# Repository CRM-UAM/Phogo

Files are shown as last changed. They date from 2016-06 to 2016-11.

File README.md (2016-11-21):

# Phogo

Phogo is an educational project to learn how to program. It is based in the [Logo](https://en.wikipedia.org/wiki/Logo_(programming_language)) programming language (and its turtle), created in 1967 by Seymour Papert and other researchers.

_Phogo es un proyecto educativo para aprender a programar basado en el lenguaje de programación [Logo](https://en.wikipedia.org/wiki/Logo_(programming_language)) (y su tortuga) creado en 1967 por Seymour Papert y otros investigadores._

**You can find more information in the [project's wiki page](https://github.com/CRM-UAM/Phogo/wiki).**
Can't find what you are looking for? [Contact us](https://github.com/CRM-UAM/Phogo/issues/new).

***Toda la documentación está en la [wiki del proyecto](https://github.com/CRM-UAM/Phogo/wiki).***
_¿No encuentras algo? [Contacta con nosotros](https://github.com/CRM-UAM/Phogo/issues/new)._

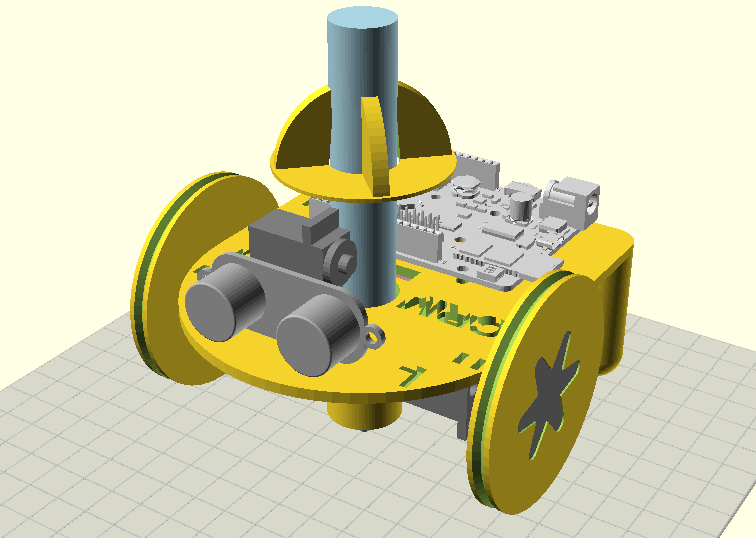
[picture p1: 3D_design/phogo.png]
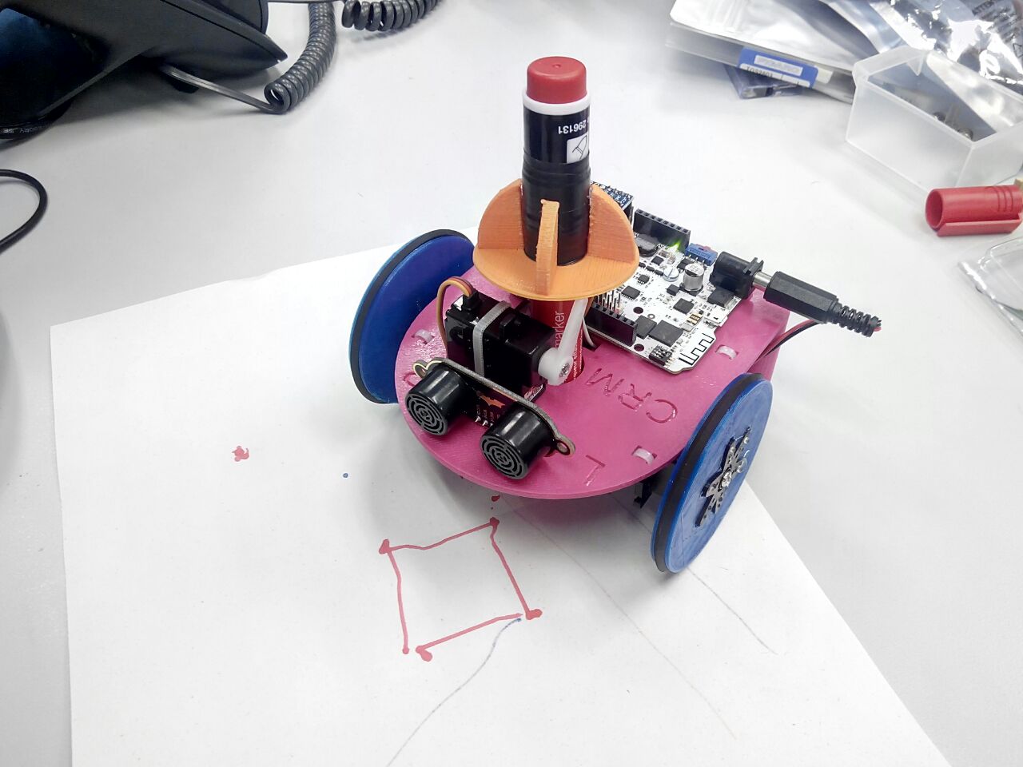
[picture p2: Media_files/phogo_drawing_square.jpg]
   
3D-printable CAD robot design. Find it in [3D_design](3D_design). _Diseño CAD imprimible en 3D. Puedes encontrarlo en [3D_design](3D_design)_

License
=

All of the Phogo source code is released under the [GNU General Public License Version 3](http://www.gnu.org/licenses/gpl-3.0.html).  
The rest of elements such as text, images or manuals are published under the [CC BY-SA 4.0 license terms](https://creativecommons.org/licenses/by-sa/4.0/).  

_Todo el código fuente de Phogo está publicado bajo una licencia [GNU General Public License Version 3](http://www.gnu.org/licenses/gpl-3.0.html)._  
_El resto de elementos como textos, imágenes o manuales bajo una licencia [CC BY-SA 4.0](https://creativecommons.org/licenses/by-sa/4.0/)._  

Authors
=

- Pablo Molins Ruano ([@molins](https://github.com/molins))
- Carlos González Sacristán ([@ChacheGS](https://github.com/ChacheGS))
- Carlos García Saura ([@CarlosGS](https://github.com/CarlosGS))

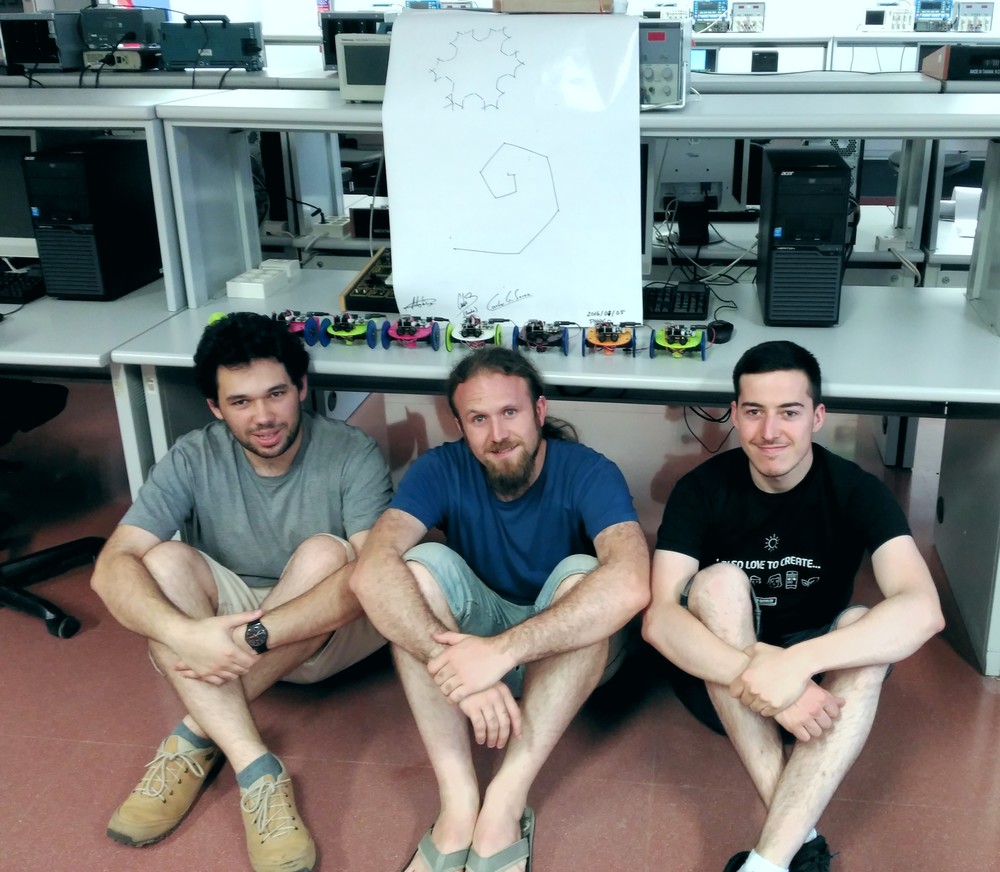
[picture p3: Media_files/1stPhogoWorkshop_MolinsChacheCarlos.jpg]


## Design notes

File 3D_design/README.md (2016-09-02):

Phogo 3D-printable design
=

Here you can find the [OpenScad](http://www.openscad.org/) source files for the Phogo mechanic parts.  
You may want to read the **[Bill of Materials & assembly guide](https://github.com/CRM-UAM/Phogo/wiki/Assembly-guide)** in the wiki.



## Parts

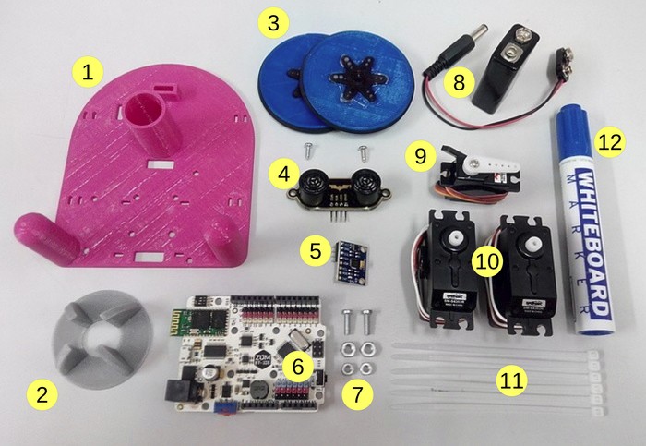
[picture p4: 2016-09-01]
Media_files/tutorial/assembly/1_all_parts_2.jpg

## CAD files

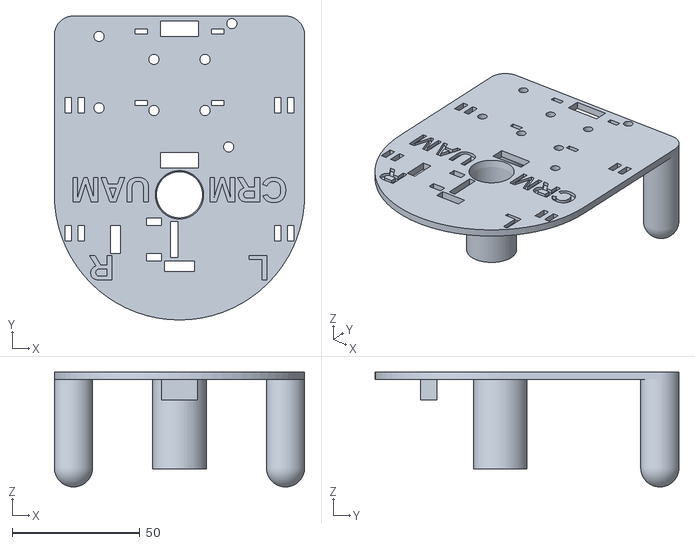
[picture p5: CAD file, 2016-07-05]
3D_design/phogo.stl
98.0 x 119.0 x 45.0

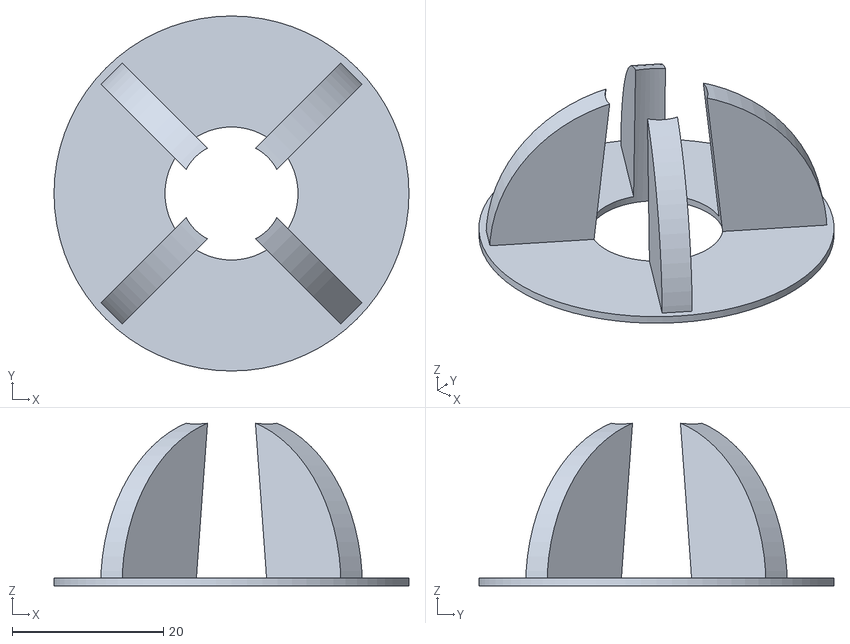
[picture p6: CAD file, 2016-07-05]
3D_design/pen_holder.stl
47.0 x 47.0 x 21.5

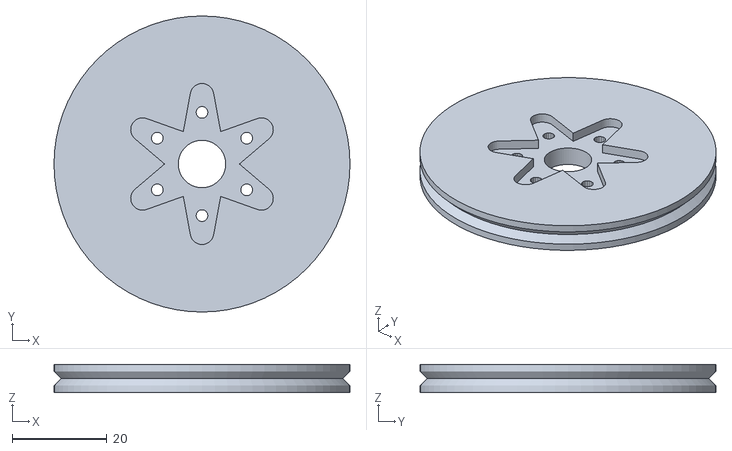
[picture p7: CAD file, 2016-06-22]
3D_design/wheel.stl
62.5 x 62.5 x 6.00

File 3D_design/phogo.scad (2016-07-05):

// This source file is part of the Phogo project
// https://github.com/CRM-UAM/Phogo
// Released under the GNU General Public License Version 3
// Club de Robotica-Mecatronica, Universidad Autonoma de Madrid, Spain



// Increase the resolution of default shapes
$fa = 5; // Minimum angle for fragments [degrees]
$fs = 0.5; // Minimum fragment size [mm]

use <libs/MCAD/servos.scad>
use <libs/Servo-wheel.scad>
use <libs/build_plate.scad>

wheel_diameter = 42;

floor_Z = -wheel_diameter;

pen_diameter = 17;
pen_len = 120;
pen_holder_tolerance = 0.5;
pen_holder_thickness = 2;
pen_holder_height = 35;
pen_tip_posZ = floor_Z;
pen_holder_Xoffset = 1;

servo_separation = 75+7;

chassis_thirdstand_diameter = 15;
chassis_thirdstand_height = -floor_Z-chassis_thirdstand_diameter/2;

chassis_thickness = 3;
chassis_width = servo_separation+2*8;
chassis_len = 70+chassis_width/2;
chassis_corner_radius = chassis_thirdstand_diameter/2;

screw_diam = 4; // diameter for tight fit

ultrasound_posY = -chassis_width/2+21;
ultrasound_support_len = 8;
ultrasound_support_X = 10;
ultrasound_support_Y = 2.5;
ultrasound_support_tolerance = 0.8;
ultrasound_support_thickness = 2;

module pen_support_vitamins() {
    color("lightblue") translate([0,0,pen_tip_posZ]) {
        translate([0,0,25]) cylinder(r=pen_diameter/2, h=pen_len-25);
        cylinder(r1=1.5,r2=pen_diameter/2+pen_holder_tolerance, h=25);
    }
    translate([-3+pen_holder_Xoffset,-8-pen_diameter/2,chassis_thickness])
        color("gray") alignds420([-18,0,17], [-90,0,-90]); // mini-servo para el rotulador
}

module pen_support(holes=false) {
    if(holes) {
        translate([0,0,pen_tip_posZ])
            cylinder(r=pen_diameter/2+pen_holder_tolerance, h=pen_len);
        cylinder(r1=pen_diameter/2+pen_holder_tolerance, r2=pen_diameter/2+2*pen_holder_tolerance, h=chassis_thickness+0.1);
        // Agujeros para sujetar el mini-servo
        translate([-3+pen_holder_Xoffset,-9-pen_diameter/2,0]) cube([3,14,chassis_thickness*3],center=true);
        translate([-11+pen_holder_Xoffset,-pen_diameter/2-2,0]) cube([6,3,chassis_thickness*3],center=true);
        translate([-11+pen_holder_Xoffset,-pen_diameter/2-16,0]) cube([6,3,chassis_thickness*3],center=true);
        // Agujero para el cable del mini-servo
        translate([-26+pen_holder_Xoffset,-9-pen_diameter/2,0]) cube([4,11,chassis_thickness*3],center=true);
        // Agujeros para los cables de la electronica
        translate([0,pen_diameter/2+pen_holder_thickness+6/2,0]) cube([15,6,chassis_thickness*3],center=true);
        translate([0,chassis_len-chassis_width/2-5,0]) cube([15,6,chassis_thickness*3],center=true);
    } else
        translate([0,0,-pen_holder_height])
            cylinder(r=pen_diameter/2+pen_holder_thickness, h=pen_holder_height+0.1);
}

module pen_holder() {
    translate([0,0,40])
        difference() {
            union() {
                cylinder(r=15+pen_diameter/2, h=1);
                difference() {
                    for(i=[-1,1]) rotate([90,0,45*i]) cylinder(r=14+pen_diameter/2, h=4, center=true);
                    rotate([180,0,0]) cylinder(r=15+pen_diameter/2, h=100);
                }
            }
            translate([0,0,-1]) cylinder(r1=pen_diameter/2+pen_holder_tolerance,r2=pen_diameter/2-4*pen_holder_tolerance, h=15+pen_diameter/2+2);
        }
    }

module continuous_rotation_servo(holes=false,wheel=false) {
    if(holes) {
        // Agujeros para las bridas
        translate([-2.5,-15,0]) cube([2.5,6,chassis_thickness*3],center=true);
        translate([2.5,-15,0]) cube([2.5,6,chassis_thickness*3],center=true);
        translate([-2.5,50-15,0]) cube([2.5,6,chassis_thickness*3],center=true);
        translate([2.5,50-15,0]) cube([2.5,6,chassis_thickness*3],center=true);
    } else {
        color("gray") futabas3003([-28,30,-20], [0,-90,180]);
        if(wheel) translate([12,0,-10]) rotate([0,90,0]) {
            Servo_wheel_6_arm_horn(); // Ruedas impresas
            color("gray") horn6(); // Soporte servo 6 brazos
        }
    }
}

module main_motors(holes=false,wheels=false) {
    translate([-servo_separation/2,0,0])
        mirror([1,0,0]) continuous_rotation_servo(holes,wheels);
    translate([servo_separation/2,0,0])
        continuous_rotation_servo(holes,wheels);
}

// From: https://github.com/Obijuan/printbot_part_library/tree/master/sensors/ultrasound
module ultrasound() {
    color("darkgray")
    translate([0,ultrasound_posY,0])
        translate([0,-4.5,14]) rotate([90,0,0]) import("libs/BAT-ultrasonic.stl");
}

module ultrasound_support(holes=false) {
    translate([0,ultrasound_posY,0])
        if(holes)
            cube([ultrasound_support_X+2*ultrasound_support_tolerance,ultrasound_support_Y+2*ultrasound_support_tolerance,ultrasound_support_len*3],center=true);
        else
            translate([0,0,-ultrasound_support_len/2+0.1]) cube([ultrasound_support_X+2*ultrasound_support_thickness,ultrasound_support_Y+2*ultrasound_support_thickness,ultrasound_support_len],center=true);
}

module battery(holes=false) {
    translate([0,50,0])
    if(holes) {
        translate([-15,14,0]) cube([5,2,chassis_thickness*3],center=true);
        translate([-15,-14,0]) cube([5,2,chassis_thickness*3],center=true);
        translate([15,14,0]) cube([5,2,chassis_thickness*3],center=true);
        translate([15,-14,0]) cube([5,2,chassis_thickness*3],center=true);
    } else {
        color("pink") translate([0,0,-15/2]) cube([52,25,15],center=true);
    }
}

// From: https://github.com/bq/zum/tree/master/zum-bt328/stl
module arduino(holes=false) {
    translate([0,43,2])
    if(holes) {
        translate([19.25,-24.25,0]) cylinder(r=screw_diam/2, h=chassis_thickness*5, center=true);
        translate([20.5,24,0]) cylinder(r=screw_diam/2, h=chassis_thickness*5, center=true);
        translate([-31.5,19,0]) cylinder(r=screw_diam/2, h=chassis_thickness*5, center=true);
        translate([-31.5,-9,0]) cylinder(r=screw_diam/2, h=chassis_thickness*5, center=true);
        for(i=[-1,1]) for(j=[-1,1]) translate([10*i,10*j,0]) cylinder(r=screw_diam/2, h=chassis_thickness*5, center=true);
    } else color("lightgray") translate([34.5,26.5,chassis_thickness+1.6]) rotate([0,0,180]) import("libs/zum_bt_328.stl");
}

module thirdstand() {
    for(i=[-1,1]) translate([i*(chassis_width/2-chassis_thirdstand_diameter/2),chassis_len-chassis_width/2-chassis_thirdstand_diameter/2,floor_Z+chassis_thirdstand_diameter/2]) union() {
            sphere(r=chassis_thirdstand_diameter/2);
            cylinder(r=chassis_thirdstand_diameter/2,h=chassis_thirdstand_height+0.1);
        }
}

module text_on_chassis() {
    translate([0,chassis_len-chassis_width/2-7,0])
    *rotate([0,0,180]) scale([1.5,1,1]) translate([0,0,chassis_thickness-1.5]) linear_extrude(height=10) {
        text("PHOGO",size=10,font="Liberation Sans",halign="center",valign="center",$fn=16);
    }
    translate([0,2,0])
    rotate([0,0,180]) translate([0,0,chassis_thickness-1.5]) linear_extrude(height=10) {
        text("CRM      UAM",size=10,font="Liberation Sans :style=Bold",halign="center",valign="center",$fn=16);
    }
    translate([0,-chassis_width/4-4,0])
    rotate([0,0,180]) translate([0,0,chassis_thickness-1.5]) linear_extrude(height=10) {
        text("L              R",size=10,font="Liberation Sans :style=Bold",halign="center",valign="center",$fn=16);
    }
}

module chassis() {
    difference() {
        union() {
            hull() {
                cylinder(r=chassis_width/2,h=chassis_thickness);
                translate([-chassis_width/2+chassis_corner_radius,chassis_len-chassis_width/2-chassis_corner_radius,0])
                    cylinder(r=chassis_corner_radius,h=chassis_thickness);
                translate([chassis_width/2-chassis_corner_radius,chassis_len-chassis_width/2-chassis_corner_radius,0])
                    cylinder(r=chassis_corner_radius,h=chassis_thickness);
            }
            pen_support();
            thirdstand();
            ultrasound_support();
        }
        pen_support(holes=true);
        main_motors(holes=true);
        ultrasound_support(holes=true);
        text_on_chassis();
        arduino(holes=true);
        battery(holes=true);
    }
}

module non_3D_printed() {
    main_motors(wheels=true);
    pen_support_vitamins();
    ultrasound();
    arduino();
    battery();
}

pen_holder();
chassis();
non_3D_printed();

//for display only, doesn't contribute to final object
translate([0,0,floor_Z]) build_plate(3,200,200);

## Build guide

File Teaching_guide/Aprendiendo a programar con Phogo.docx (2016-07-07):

# Aprendiendo a programar con Phogo

¿Alguna vez te has preguntado cómo es posible que Google sepa dónde encontrar cualquier cosa que busques en Internet? ¿Te has preguntado cómo funciona Minecraft? ¿Cómo sabe tu lavadora qué hacer para dejar tu ropa limpia? Son tres situaciones muy distintas pero las tres tienen en común la programación. Para que las tres funcionen, alguien ha programado un ordenador.

Programar es lo que hacemos los informáticos para dar instrucciones a un ordenador. Le decimos al ordenador qué tiene que hacer. Y el ordenador, si se lo hemos explicado bien, hace exactamente lo que le hemos dicho. Ahora vamos a aprender cómo hablarle al ordenador para que entienda.

Los ordenadores son como las personas en muchos aspectos. Por ejemplo, solo nos harán caso si hablamos un lenguaje que entiendan. Si a ti te hablan en chino, no harás caso, porque no entiendes chino. Si a un ordenador le hablas en español, no te entiende. Por eso nos toca aprender un nuevo lenguaje para hablar con el ordenador.

El lenguaje que vamos a aprender se llama Python. Se parece un poquito al inglés, pero solo un poco. Para que sea más divertido, al ordenador le hemos dado una tortuga. La tortuga es tan obediente como el ordenador. ¡Si sabemos cómo darle órdenes!

Aquí van dos foto de la tortuga. La tuya puede que tenga un color distinto, pero es igual en todo lo demás:

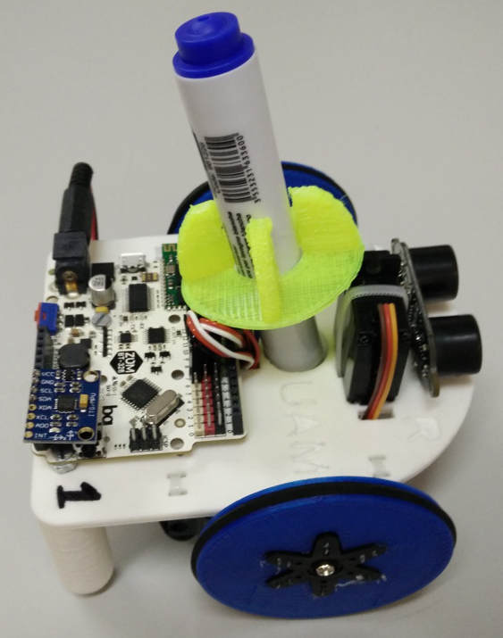
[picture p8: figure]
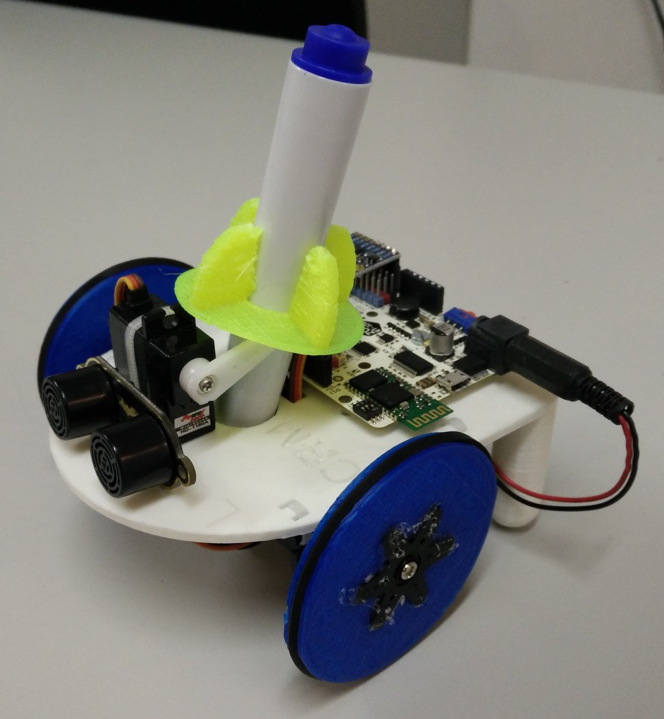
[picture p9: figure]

# Cómo hablar con el ordenador

Para hablar con el ordenador vamos a usar un programa que se llama Idle. Ya deberías tenerlo abierto en tu ordenador. Si no está abierto, o se cerrara en algún momento, pide ayuda a un monitor para volver a abrirlo.

El programa tiene dos ventanas:

1. A la derecha, la ventana de instrucciones, donde tú escribirás lo que quieras decirle al ordenador.
2. A la izquierda, la ventana de resultados, donde el ordenador te dirá qué va haciendo.

¿Has visto que en la ventana de instrucciones, arriba del todo, aparece from crmphogo import *? A esa frase la llamamos el saludo. Es importante que aparezca en todos los programas que escribas que quieran hablar con la tortuga, porque es la manera que tenemos de decirle al ordenador que queremos hablar con la tortuga. Si no lo ponemos y le damos órdenes para la tortuga, el ordenador no nos entenderá y nos dirá que no nos entiende la ventana de resultados.

Recuerda que el ordenador habla un idioma raro. Si aparece algo en la ventana de resultados que no entiendes y la tortuga no hace lo que quieres, pregunta a un monitor, que sabe cómo entender al ordenador.

Hemos aprendido ya muchas cosas:

- Que en el programa hay dos ventas:
  1. A la derecha, la venta de instrucciones, donde le contamos al ordenador qué tiene que hacer.
  2. A la izquierda, la venta de resultados, donde el ordenador nos cuenta qué tal le va cumpliendo nuestras órdenes.
- La tortuga necesita un saludo cada vez: from crmphogo import *
- Si tenemos algún problema, podemos pedir ayuda a los monitores, en cualquier momento

# Aprendiendo a moverse

Vamos a empezar con algo fácil. Vamos a hacer que la tortuga se mueva. Prueba a escribir forward() en la ventana de instrucciones, debajo del saludo. forward() en inglés significa “hacia delante” (así que la tortuga debería moverse hacia delante). Cuando lo hayas escrito, deberías tener algo así en tu ventana de instrucciones:

from crmphogo import *

forward()

Una vez hemos terminado de escribir tenemos que decirle al ordenador que ya hemos terminado y queremos que empiece a hacer lo que hemos puesto. Para eso, pulsa F5 (una tecla que está arriba en tu teclado). Deberías ver en la ventana de resultados una tortuga dibujada y al ordenador diciéndole a la tortuga que tiene que ir hacia delante (FD en el lenguaje de la tortuga). Cuando la tortuga termine de andar, le dirá que todo ha ido bien. Le dirá OK al ordenador.

¿Se ha movido la tortuga? Si no lo ha hecho, pide ayuda a alguno de los monitores. Si lo ha hecho… ¡has escrito tu primer programa!

La tortuga, como toda tortuga que se precie, no sólo puede moverse hacia delante. Borra forward() y prueba a escribir back(). Deberías tener algo así en tu ventana de instrucciones:

from crmphogo import *

back()

Fíjate que seguimos poniendo el saludo. Es importante que lo pongamos cada vez. ¿Qué ha hecho la tortuga? ¿Y qué pasa cuando borras back() y escribes right() o left()? ¡Pruébalo! Y recuerda pulsar F5 cada vez que quieras que el ordenador haga lo que hayas escrito en la ventana de instrucciones.

Si la tortuga solo pudiera girar 90º grados sería una tortuga mala. Como la nuestra no es una tortuga mala, puede girar tantos grados como quieras. ¿Cómo? Prueba a escribir en tu ventana de instrucciones lo siguientes:

from crmphogo import *

right(45)

left(180)

right(270)

Y fíjate en lo que pasa…

forward() y back() también pueden escribirse con un número dentro. Prueba a que tu ventana de instrucciones tenga el siguiente código:

from crmphogo import *

forward(5)

back(20)

forward(15)

Y observa qué ocurre…

Si has llegado hasta aquí, ahora sabrás cómo mover a la tortuga:

- Si escribes forward() avanzará.
- Si escribes back(), retrocederá.
- Si escribes right() girará a la derecha
- Con left() girará a la izquierda.

También sabrás que puedes escribir las ordenes con más información:

- Si escribes right(grados) la tortuga girará hacia la derecha tantos grados como hayas dicho.
- Si no pones nada, girará 90º.
- Lo mismo con left() (pero girando a la izquierda).
- foward(número) avanzan tantos centímetros como le hayas dicho.
- Si no escribes un número avanzará 10 cm.
- Igual para back() (solo que yendo hacia atrás).

# Aprendiendo a dibujar

Que la tortuga se mueva es divertido, pero más divertido es que pinte. Si te fijas en tu tortuga, tiene un rotulador. Podemos pedirle a la tortuga que utilice el rotulador para ir pintando allí por donde vaya. Vamos a probarlo.

Asegúrate de que tu tortuga está encima de un papel. Escribe, justo después del saludo, pen_down() y luego algo que haga que la tortuga se mueva. pen_down() significa “rotulador abajo” y es la manera de decirle a la tortuga que vaya pintando.

Con esto, ¿sabrías cómo dibujar un cuadrado? ¡Inténtalo!

Puede que en algunos dibujos, quieras que la tortuga se mueva por algún sitio sin dejar rastro. Que deje de pintar. Para eso escribe pen_up() que significa “rotulador arriba”. Al subirlo deja de apoyarse en el papel, y ya no se ve.

¿Podrías dibujar un cuadrado, pero ahora con líneas discontinuas? Algo así:

Con esto puedes dibujar muchas cosas distintas. ¡A ver qué se te ocurre! Dibuja todas ellas. Mira que ha hecho el resto, y si hay algo te gusta, ¡intenta dibujarlo tú!

La tortuga ya no solo se mueve, ¡ahora también dibuja!

- Si escribes pen_down() empezará a dibujar.
- Si escribes pen_up() dejará de hacerlo.

Acuérdate de poner la tortuga sobre papel, si va a pintar.

# Aprendiendo a repetir

Nota: Esta parte puede ser un poco complicada. Léela solo si quieres. Pregunta si tienes dudas.

¿Te acuerdas del cuadrado que has hecho al principio? Debes haber escrito en la ventana de instrucciones algo parecido a esto:

from crmphogo import *

forward()

right()

forward()

right()

forward()

right()

forward()

right()

Te has fijado en que las líneas se repiten, ¿verdad? Hay una manera de escribir esto mismo, pero de una manera más corta. Le podemos decir al ordenador que él repita cosas por nosotros.

Existe una palabra para ello: while. En inglés signfica “mientras” y la vamos a usar para decirle al ordenador que siga haciendo algo mientras algo ocurra. Vamos a ver mejor un ejemplo:

from crmphogo import *

veces = 1

while veces <= 4:

forward()

rigth()

veces = veces + 1

Como ves, es más corto que lo de antes ¡y también hace un cuadrado! El único problema que tiene es que todavía no lo entendemos… ¡pero por poco tiempo! Pruébalo. Para lograr que las últimas líneas salgan desplazadas a la derecha, utiliza la tecla del tabulador, que ese esa con una flecha a la derecha y a la izquierda que está a la izquierda del teclado, encima de la de mayúsculas.

La línea que dice veces = 1 le está diciendo al ordenador que recuerde que cuando aparezca la palabra veces él tiene que pensar en un 1. Así, cuando lee while veces <= 4 el ordenador leerá while 1 <= 4, es decir, “mientras 1 sea menor o igual que 4”. Como el 1 es menor que el 4, ejecutará lo que hay dentro del while, es decir, las líneas que están debajo que están metidas a la derecha. Avanzará, girará y le dirá al ordenador que veces ahora será veces + 1, es decir, 1 + 1, es decir, ahora le decimos que veces es 2.

Cuando termina, el ordenador vuelve al while para mirar si todavía sigue siendo verdad. while veces <= 4 es “mientras veces sea menor o igual a 4” que como veces es 2, sigue siendo verdad. De nuevo vuelve a avanzar, girar y veces ahora vale 3. 3 es menor que 4, así que otra vez: avanzar, girar y ahora veces es 4. Vuelve a comprobar y como veces vale 4 todavía lo hace una vez más: avanza, girar y ahora veces es 5. Cuando vuelve al while, ¡esta vez ya no es verdad! Como 5 no es mayor o igual que 4, ya no hace más lo que aparece dentro.

Piensa en otras cosas que has escrito antes, y cómo podrías utilizar el while para ahórrate escribir cosas.

Si queremos repetir algo, no hace falta que lo escribamos varias veces:

- Si escribimos while condición la tortuga hará lo que pone dentro mientras la condición sea verdad.
- Para que funcione, tenemos que escribir : después de la condición, y todo lo que queremos que haga debajo, poniendo un tabulador delante de cada línea.

Pero el ordenador tiene una manera más chula de repetir. Con lo que hemos escrito antes, hemos dibujado un cuadrado. Y sería muy útil poder enseñarle a la tortuga que si le pedimos un cuadrado, queremos que haga eso, ¿no? ¡Pues se puede!

¿Qué haces tú cuando no conoces una palabra que es nueva? Le pides a alguien que te la defina, o miras su definición en un diccionario. Utilizas palabras que ya sabes para aprender palabras nuevas. Pues la tortuga funciona igual.

Vamos a definirle qué es un cuadrado. Para ello, usamos la palabra def, que es una manera corta de decir “definition”, que en inglés significa “definición”.

Si ponemos def nombre(): la tortuga mirará que hay debajo y se aprenderá que cuando le escribas nombre() quiere que hagas lo que pusiste antes debajo. Siguiendo con el ejemplo del cuadrado, si queremos que la tortuga aprenda lo que es un cuadrado, se lo definimos:

from crmphogo import *

def cuadrado():

veces = 1

while veces <= 4:

forward()

rigth()

veces = veces + 1

Prueba a escribir esto y mira qué pasa… ¿Pasa algo cuando le das a F5? Pues no. Porque hemos definido que es un cuadrado, ¡pero no lo hemos utilizado! Escribe al final del todo cuadrado()…

Es importante que sepas que la tortuga tiene muy mala memoria y olvida las definiciones cada vez. Si quieres usar una definición, tienes que recordársela, debajo del saludo y antes de utilizarla. Si no lo haces, no sabrá de qué estás hablando… Si borras todo para hacer algo nuevo, recuerda no borrar las definiciones, para que todavía te sirvan.

La tortuga, como nosotros, puede aprender palabras nuevas si se las definimos:

- Si escribimos def nombre() la tortuga recordará que cuando pones nombre, quieres que haga lo que pone debajo.
- Para que funcione, tenemos que escribir : después del nombre y lo que queremos que haga debajo, poniendo un tabulador delante de cada línea.

# Aprendiendo a usar los ojos

Nota: Esta parte puede ser un poco complicada. Léela solo si quieres. Pregunta si tienes dudas.

Si te has fijado, la tortuga tiene unos ojos en la parte de delante. No son unos ojos como los nuestros, pero le sirven para ver si hay algo delante de ella y así poder esquivarlo.

Si escribimos obstacle() en la ventana de instrucciones, la tortuga nos dirá a qué distancia se encuentra el objeto que esté delante de ella. Pon la tortuga delante de una obstáculo y prueba esto:

from crmphogo import *

obstacle()

En la ventana de resultados, verás que sale un número. Son los centímetros a los que está el obstáculo. Prueba a separar la tortuga del obstáculo y repite. ¿Qué le pasa al número? ¿Cambia o se queda igual?

Aunque es útil que la tortuga nos diga a qué distancia están los obstáculos, sería más útil que le pudiéramos decir a la tortuga que hiciera cosas distintas si hay un obstáculo y si no lo hay. Por ejemplo, si no hay un obstáculo, que avance, y si hay un obstáculo, que dé la vuelta y se aleje del obstáculo.

Para eso podemos escribir lo que se llaman condiciones. Una condición es cuando le decimos a la tortuga que haga una cosa u otra dependiendo de si algo ocurre. Si te fijas, hemos usado mucho la palabras “si” cuando lo explicábamos. En inglés, “si” se traduce por if y ¡es exactamente lo que necesitamos!

Vamos a decirle a la tortuga que avance, pero solo si no hay ningún obstáculo. Si hay un obstáculo, que se dé la vuelta y luego avance. Escribe esto en tu ventana de instrucciones:

from crmphogo import *

if obstacle() < 10:

right(180)

forward()

Cuando decimos que if obstacle() < 10: estamos diciendo que “si hay un obstáculo a menos de 10 cm” haga lo que pone justo dentro (para eso ponemos los dos puntos, para que mire lo que hay dentro). ¿Y qué es dentro? Fíjate que la siguiente orden, right(180), no empieza a la misma altura que las demás, sino que tiene espacios delante. Eso es porque está dentro del if. Eso significa que sólo deberá girar 180º si hay un obstáculo a menos de 10 cm. La tortuga después avanzará, haya o no haya delante un obstáculo. Si lo hay habrá girado antes de hacerlo. Pruébalo, poniendo la tortuga delante de una pared y con espacio delante, para ver qué pasa.

Resulta que la tortuga tiene ojos. Y los puede usar para ver si hay algo delante:

- Si escribimos obstacle(), la tortuga nos dirá a cuántos centímetros hay un obstáculo delante.

Además, también podemos pedirle que tome decisiones:

- Si escribimos if condición la tortuga hará lo que pone dentro solo si la condición es verdad.
- Para que funcione, tenemos que escribir : después de la condición, y todo lo que queremos que haga debajo separado con cuatro espacios.

# Ahora, a explorar

Ya sabes todo lo que puedes pedirle a la tortuga que haga, ¡e incluso cómo lograr que aprenda cosas nuevas! Ahora, te toca ponerlo a prueba, y hacer todo lo que te apetezca. Dibujar una estrella, enseñar a la tortuga a salir de un laberinto, escribir tu nombre… ¡las opciones son infinitas y ya eres un programador!

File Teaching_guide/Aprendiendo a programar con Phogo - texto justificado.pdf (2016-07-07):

## APRENDIENDO A PROGRAMAR CON PHOGO

¿Alguna vez te has preguntado cómo es posible que Google sepa dónde encontrar cualquier cosa que busques en Internet? ¿Te has preguntado cómo funciona Minecraft? ¿Cómo sabe tu lavadora qué hacer para dejar tu ropa limpia? Son tres situaciones muy distintas pero las tres tienen en común la programación. Para que las tres funcionen, alguien ha programado un ordenador.

Programar es lo que hacemos los informáticos para dar instrucciones a un ordenador. Le decimos al ordenador qué tiene que hacer. Y el ordenador, si se lo hemos explicado bien, hace exactamente lo que le hemos dicho. Ahora vamos a aprender cómo hablarle al ordenador para que entienda.

Los ordenadores son como las personas en muchos aspectos. Por ejemplo, solo nos harán caso si hablamos un lenguaje que entiendan. Si a ti te hablan en chino, no harás caso, porque no entiendes chino. Si a un ordenador le hablas en español, no te entiende. Por eso nos toca aprender un nuevo lenguaje para hablar con el ordenador.

El lenguaje que vamos a aprender se llama Python. Se parece un poquito al inglés, pero solo un poco. Para que sea más divertido, al ordenador le hemos dado una tortuga. La tortuga es tan obediente como el ordenador. ¡Si sabemos cómo darle órdenes!

Aquí van dos foto de la tortuga. La tuya puede que tenga un color distinto, pero es igual en todo lo demás:

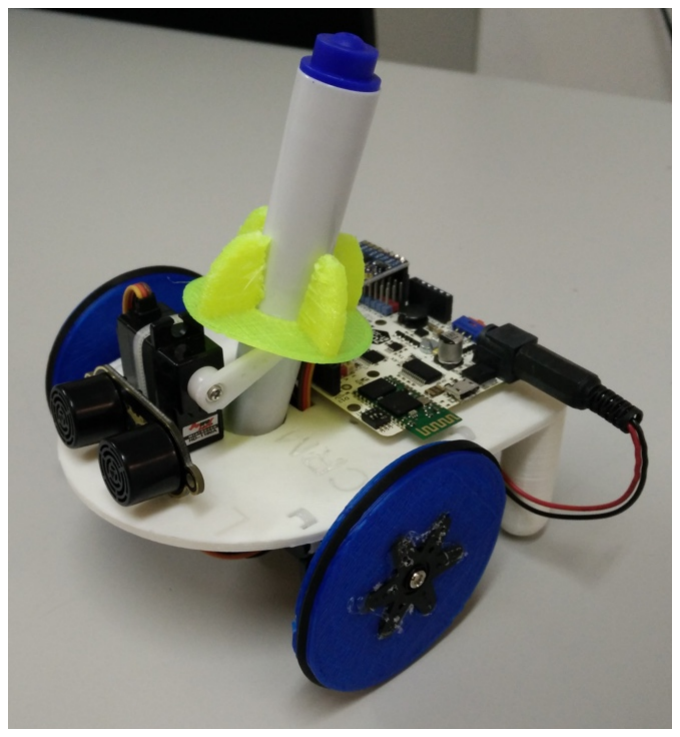
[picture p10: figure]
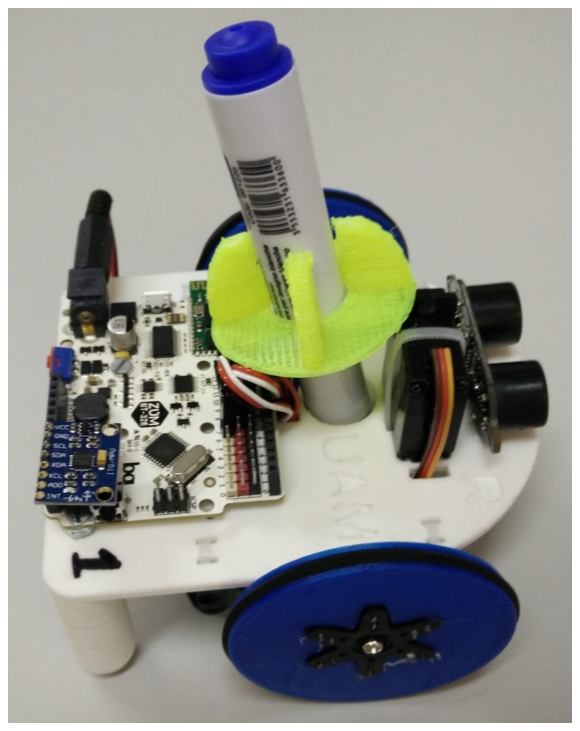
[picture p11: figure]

CÓMO HABLAR CON EL ORDENADOR

Para hablar con el ordenador vamos a usar un programa que se llama Idle. Ya deberías tenerlo abierto en tu ordenador. Si no está abierto, o se cerrara en algún momento, pide ayuda a un monitor para volver a abrirlo.

El programa tiene dos ventanas:

1. A la derecha, la ventana de instrucciones, donde tú escribirás lo que quieras decirle al ordenador.
2. A la izquierda, la ventana de resultados, donde el ordenador te dirá qué va haciendo.

¿Has visto que en la ventana de instrucciones, arriba del todo, aparece from crmphogo import *? A esa frase la llamamos el saludo. Es importante que aparezca en todos los programas que escribas que quieran hablar con la tortuga, porque es la manera que tenemos de decirle al ordenador que queremos hablar con la tortuga. Si no lo ponemos y le damos órdenes para la tortuga, el ordenador no nos entenderá y nos dirá que no nos entiende la ventana de resultados.

Recuerda que el ordenador habla un idioma raro. Si aparece algo en la ventana de resultados que no entiendes y la tortuga no hace lo que quieres, pregunta a un monitor, que sabe cómo entender al ordenador.

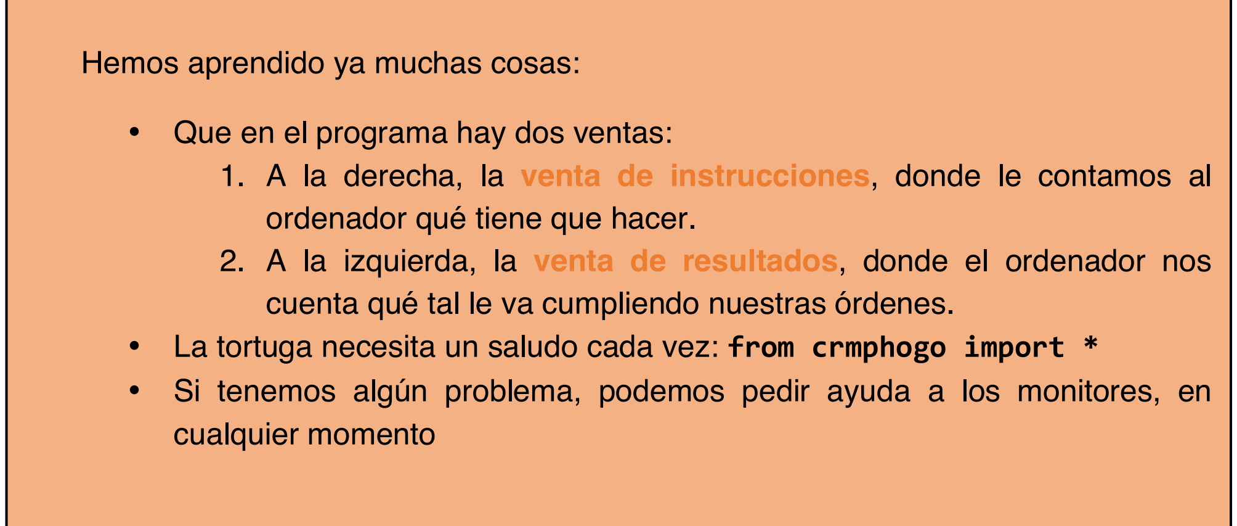
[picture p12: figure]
Hemos aprendido ya muchas cosas:; • Que en el programa hay dos ventas:; ordenador qué tiene que hacer.; cualquier momento

1. A la derecha, la venta de instrucciones, donde le contamos al
2. A la izquierda, la venta de resultados, donde el ordenador nos cuenta qué tal le va cumpliendo nuestras órdenes.
- La tortuga necesita un saludo cada vez: from crmphogo import *
- Si tenemos algún problema, podemos pedir ayuda a los monitores, en

APRENDIENDO A MOVERSE

Vamos a empezar con algo fácil. Vamos a hacer que la tortuga se mueva. Prueba a escribir forward() en la ventana de instrucciones, debajo del saludo. forward() en inglés significa “hacia delante” (así que la tortuga debería moverse hacia delante). Cuando lo hayas escrito, deberías tener algo así en tu ventana de instrucciones:

from crmphogo import *

forward()

Una vez hemos terminado de escribir tenemos que decirle al ordenador que ya hemos terminado y queremos que empiece a hacer lo que hemos puesto. Para eso, pulsa F5 (una tecla que está arriba en tu teclado). Deberías ver en la ventana de resultados una tortuga dibujada y al ordenador diciéndole a la tortuga que tiene que ir hacia delante (FD en el lenguaje de la tortuga). Cuando la tortuga termine de andar, le dirá que todo ha ido bien. Le dirá OK al ordenador.

¿Se ha movido la tortuga? Si no lo ha hecho, pide ayuda a alguno de los monitores. Si lo ha hecho… ¡has escrito tu primer programa!

La tortuga, como toda tortuga que se precie, no sólo puede moverse hacia delante. Borra forward() y prueba a escribir back(). Deberías tener algo así en tu ventana de instrucciones:

from crmphogo import *

back()

Fíjate que seguimos poniendo el saludo. Es importante que lo pongamos cada vez. ¿Qué ha hecho la tortuga? ¿Y qué pasa cuando borras back() y escribes right() o left()? ¡Pruébalo! Y recuerda pulsar F5 cada vez que quieras que el ordenador haga lo que hayas escrito en la ventana de instrucciones.

Si la tortuga solo pudiera girar 90º grados sería una tortuga mala. Como la nuestra no es una tortuga mala, puede girar tantos grados como quieras. ¿Cómo? Prueba a escribir en tu ventana de instrucciones lo siguientes:

from crmphogo import *

right(45)

left(180)

right(270)

Y fíjate en lo que pasa…

forward() y back() también pueden escribirse con un número dentro. Prueba a que tu ventana de instrucciones tenga el siguiente código:

from crmphogo import *

forward(5)

back(20)

forward(15)

Y observa qué ocurre…

Si has llegado hasta aquí, ahora sabrás cómo mover a la tortuga:

- Si escribes forward() avanzará.
- Si escribes back(), retrocederá.
- Si escribes right() girará a la derecha
- Con left() girará a la izquierda.

También sabrás que puedes escribir las ordenes con más información:

- Si escribes right(grados) la tortuga girará hacia la derecha tantos grados como hayas dicho.
- Si no pones nada, girará 90º.
- Lo mismo con left() (pero girando a la izquierda).
- foward(número) avanzan tantos centímetros como le hayas dicho.
- Si no escribes un número avanzará 10 cm.
- Igual para back() (solo que yendo hacia atrás).

APRENDIENDO A DIBUJAR

Que la tortuga se mueva es divertido, pero más divertido es que pinte. Si te fijas en tu tortuga, tiene un rotulador. Podemos pedirle a la tortuga que utilice el rotulador para ir pintando allí por donde vaya. Vamos a probarlo.

Asegúrate de que tu tortuga está encima de un papel. Escribe, justo después del saludo, pen_down() y luego algo que haga que la tortuga se mueva. pen_down() significa “rotulador abajo” y es la manera de decirle a la tortuga que vaya pintando.

Con esto, ¿sabrías cómo dibujar un cuadrado? ¡Inténtalo!

Puede que en algunos dibujos, quieras que la tortuga se mueva por algún sitio sin dejar rastro. Que deje de pintar. Para eso escribe pen_up() que significa “rotulador arriba”. Al subirlo deja de apoyarse en el papel, y ya no se ve.

¿Podrías dibujar un cuadrado, pero ahora con líneas discontinuas? Algo así:

Con esto puedes dibujar muchas cosas distintas. ¡A ver qué se te ocurre! Dibuja todas ellas. Mira que ha hecho el resto, y si hay algo te gusta, ¡intenta dibujarlo tú!

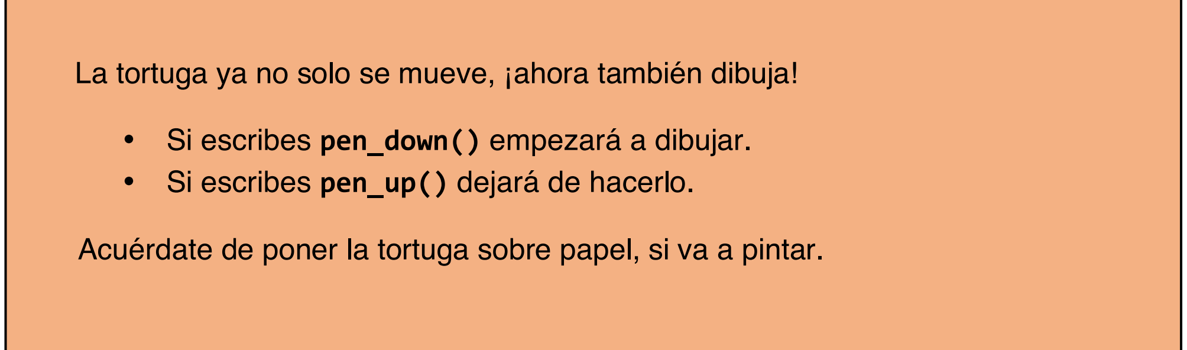
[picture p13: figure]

La tortuga ya no solo se mueve, ¡ahora también dibuja!

- Si escribes pen_down() empezará a dibujar.
- Si escribes pen_up() dejará de hacerlo.

Acuérdate de poner la tortuga sobre papel, si va a pintar.

APRENDIENDO A REPETIR

Nota: Esta parte puede ser un poco complicada. Léela solo si quieres. Pregunta si tienes dudas.

¿Te acuerdas del cuadrado que has hecho al principio? Debes haber escrito en la ventana de instrucciones algo parecido a esto:

from crmphogo import *

forward()

right()

forward()

right()

forward()

right()

forward()

right()

Te has fijado en que las líneas se repiten, ¿verdad? Hay una manera de escribir esto mismo, pero de una manera más corta. Le podemos decir al ordenador que él repita cosas por nosotros.

Existe una palabra para ello: while. En inglés signfica “mientras” y la vamos a usar para decirle al ordenador que siga haciendo algo mientras algo ocurra. Vamos a ver mejor un ejemplo:

from crmphogo import *

veces = 1

while veces <= 4:

forward()

rigth()

veces = veces + 1

Como ves, es más corto que lo de antes ¡y también hace un cuadrado! El único problema que tiene es que todavía no lo entendemos… ¡pero por poco tiempo! Pruébalo. Para lograr que las últimas líneas salgan desplazadas a la derecha, utiliza la tecla del tabulador, que ese esa con una flecha a la derecha y a la izquierda que está a la izquierda del teclado, encima de la de mayúsculas.

La línea que dice veces = 1 le está diciendo al ordenador que recuerde que cuando aparezca la palabra veces él tiene que pensar en un 1. Así, cuando lee while veces <= 4 el ordenador leerá while 1 <= 4, es decir, “mientras 1 sea menor o igual que 4”. Como el 1 es menor que el 4, ejecutará lo que hay dentro del while, es decir, las líneas que están debajo que están metidas a la derecha. Avanzará, girará y le dirá al ordenador que veces ahora será veces + 1, es decir, 1 + 1, es decir, ahora le decimos que veces es 2.

Cuando termina, el ordenador vuelve al while para mirar si todavía sigue siendo verdad. while veces <= 4 es “mientras veces sea menor o igual a 4” que como veces es 2, sigue siendo verdad. De nuevo vuelve a avanzar, girar y veces ahora vale 3. 3 es menor que 4, así que otra vez: avanzar, girar y ahora veces es 4. Vuelve a comprobar y como veces vale 4 todavía lo hace una vez más: avanza, girar y ahora veces es 5. Cuando vuelve al while, ¡esta vez ya no es verdad! Como 5 no es mayor o igual que 4, ya no hace más lo que aparece dentro.

Piensa en otras cosas que has escrito antes, y cómo podrías utilizar el while para ahórrate escribir cosas.

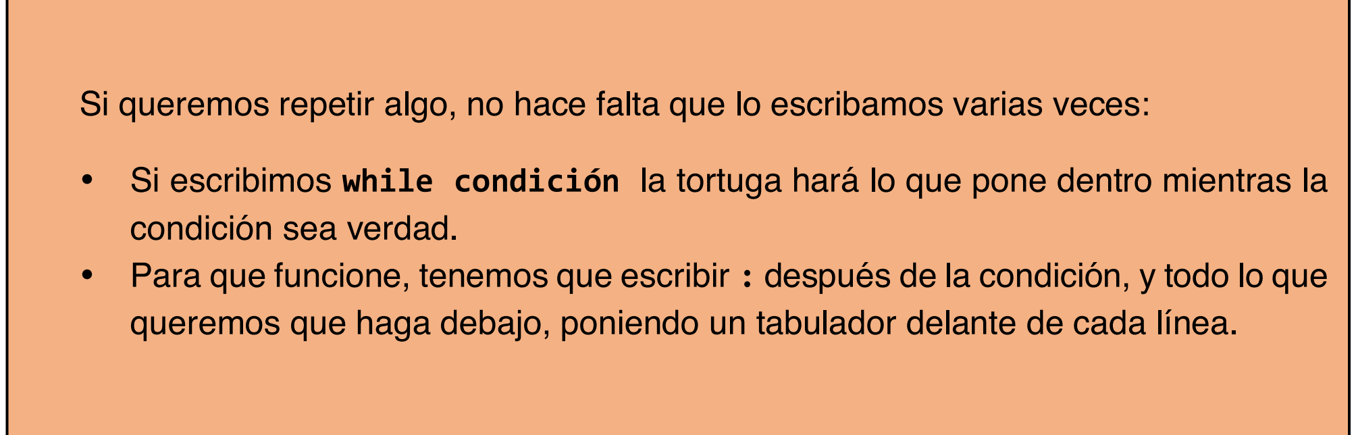
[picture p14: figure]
condición sea verdad.

Pero el ordenador tiene una manera más chula de repetir. Con lo que hemos escrito antes, hemos dibujado un cuadrado. Y sería muy útil poder enseñarle a la tortuga que si le pedimos un cuadrado, queremos que haga eso, ¿no? ¡Pues se puede!

¿Qué haces tú cuando no conoces una palabra que es nueva? Le pides a

Si queremos repetir algo, no hace falta que lo escribamos varias veces:

- Si escribimos while condición la tortuga hará lo que pone dentro mientras la
- Para que funcione, tenemos que escribir : después de la condición, y todo lo que queremos que haga debajo, poniendo un tabulador delante de cada línea.

alguien que te la defina, o miras su definición en un diccionario. Utilizas palabras que ya sabes para aprender palabras nuevas. Pues la tortuga funciona igual.

Vamos a definirle qué es un cuadrado. Para ello, usamos la palabra def, que es una manera corta de decir “definition”, que en inglés significa “definición”.

Si ponemos def nombre(): la tortuga mirará que hay debajo y se aprenderá que cuando le escribas nombre() quiere que hagas lo que pusiste antes debajo. Siguiendo con el ejemplo del cuadrado, si queremos que la tortuga aprenda lo que es un cuadrado, se lo definimos:

from crmphogo import *

def cuadrado():

veces = 1

while veces <= 4:

forward()

rigth()

veces = veces + 1

Prueba a escribir esto y mira qué pasa… ¿Pasa algo cuando le das a F5? Pues no. Porque hemos definido que es un cuadrado, ¡pero no lo hemos utilizado! Escribe al final del todo cuadrado()…

Es importante que sepas que la tortuga tiene muy mala memoria y olvida las definiciones cada vez. Si quieres usar una definición, tienes que recordársela, debajo del saludo y antes de utilizarla. Si no lo haces, no sabrá de qué estás hablando… Si borras todo para hacer algo nuevo, recuerda no borrar las definiciones, para que todavía te sirvan.

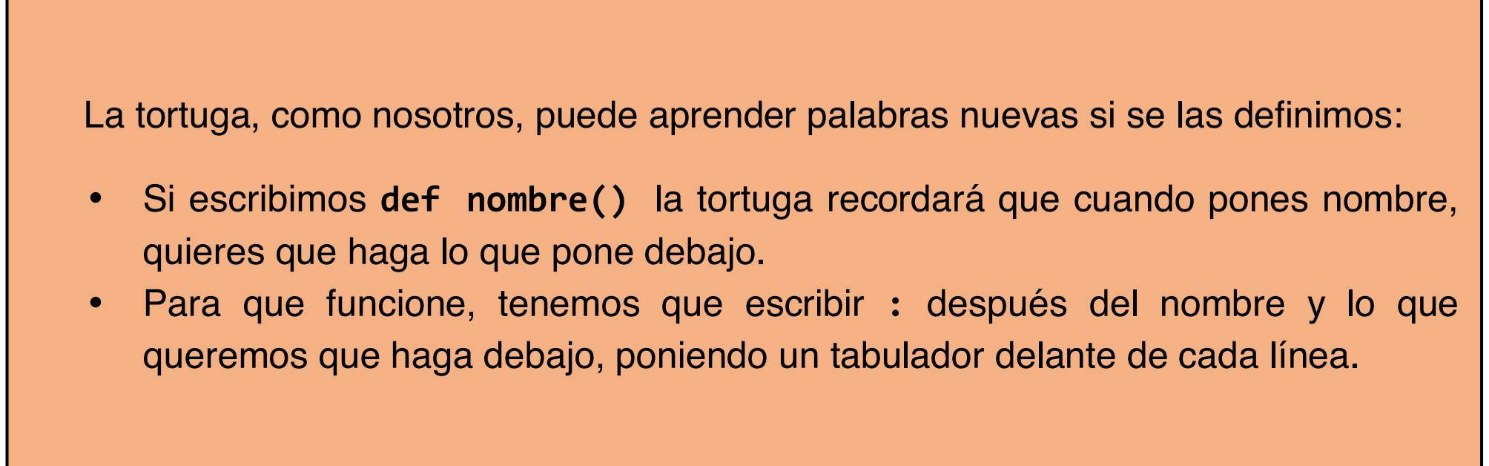
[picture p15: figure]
quieres que haga lo que pone debajo.

APRENDIENDO A USAR LOS OJOS

La tortuga, como nosotros, puede aprender palabras nuevas si se las definimos:

- Si escribimos def nombre() la tortuga recordará que cuando pones nombre,
- Para que funcione, tenemos que escribir : después del nombre y lo que queremos que haga debajo, poniendo un tabulador delante de cada línea.

Nota: Esta parte puede ser un poco complicada. Léela solo si quieres. Pregunta si tienes dudas.

Si te has fijado, la tortuga tiene unos ojos en la parte de delante. No son unos ojos como los nuestros, pero le sirven para ver si hay algo delante de ella y así poder esquivarlo.

Si escribimos obstacle() en la ventana de instrucciones, la tortuga nos dirá a qué distancia se encuentra el objeto que esté delante de ella. Pon la tortuga delante de una obstáculo y prueba esto:

from crmphogo import *

obstacle()

En la ventana de resultados, verás que sale un número. Son los centímetros a los que está el obstáculo. Prueba a separar la tortuga del obstáculo y repite. ¿Qué le pasa al número? ¿Cambia o se queda igual?

Aunque es útil que la tortuga nos diga a qué distancia están los obstáculos, sería más útil que le pudiéramos decir a la tortuga que hiciera cosas distintas si hay un obstáculo y si no lo hay. Por ejemplo, si no hay un obstáculo, que avance, y si hay un obstáculo, que dé la vuelta y se aleje del obstáculo.

Para eso podemos escribir lo que se llaman condiciones. Una condición es cuando le decimos a la tortuga que haga una cosa u otra dependiendo de si algo ocurre. Si te fijas, hemos usado mucho la palabras “si” cuando lo explicábamos. En inglés, “si” se traduce por if y ¡es exactamente lo que necesitamos!

Vamos a decirle a la tortuga que avance, pero solo si no hay ningún obstáculo. Si hay un obstáculo, que se dé la vuelta y luego avance. Escribe esto en tu ventana de instrucciones:

from crmphogo import *

if obstacle() < 10:

right(180)

forward()

Cuando decimos que if obstacle() < 10: estamos diciendo que “si hay un obstáculo a menos de 10 cm” haga lo que pone justo dentro (para eso ponemos los dos puntos, para que mire lo que hay dentro). ¿Y qué es dentro?

Fíjate que la siguiente orden, right(180), no empieza a la misma altura que las demás, sino que tiene espacios delante. Eso es porque está dentro del if. Eso significa que sólo deberá girar 180º si hay un obstáculo a menos de 10 cm. La tortuga después avanzará, haya o no haya delante un obstáculo. Si lo hay habrá girado antes de hacerlo. Pruébalo, poniendo la tortuga delante de una pared y con espacio delante, para ver qué pasa.

AHORA, A EXPLORAR

Ya sabes todo lo que puedes pedirle a la tortuga que haga, ¡e incluso cómo lograr que aprenda cosas nuevas! Ahora, te toca ponerlo a prueba, y hacer todo lo que te apetezca. Dibujar una estrella, enseñar a la tortuga a salir de un laberinto, escribir tu nombre… ¡las opciones son infinitas y ya eres un programador!

Resulta que la tortuga tiene ojos. Y los puede usar para ver si hay algo delante:

- Si escribimos obstacle(), la tortuga nos dirá a cuántos centímetros hay un obstáculo delante.

Además, también podemos pedirle que tome decisiones:

- Si escribimos if condición la tortuga hará lo que pone dentro solo si la condición es verdad.
- Para que funcione, tenemos que escribir : después de la condición, y todo lo que queremos que haga debajo separado con cuatro espacios.

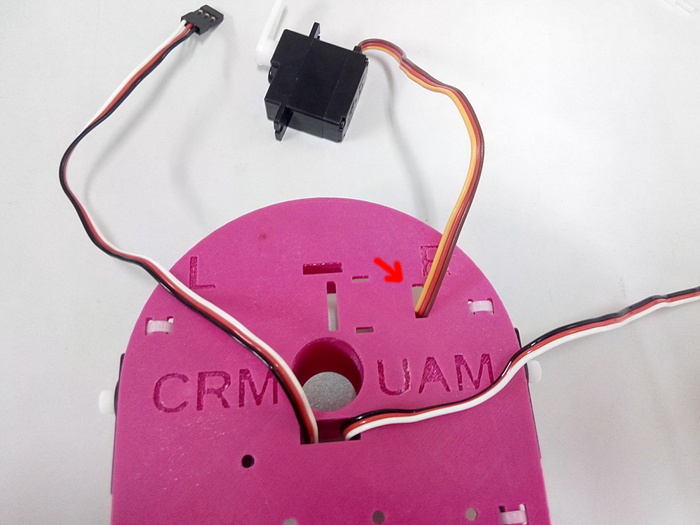
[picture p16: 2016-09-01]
Media_files/tutorial/assembly/3_penServo_2.jpg

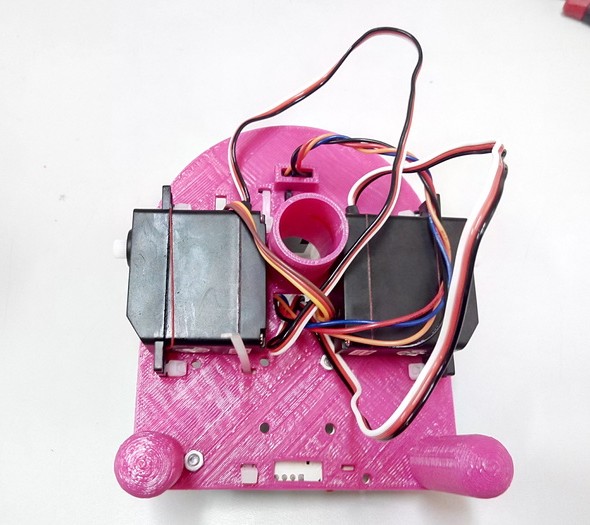
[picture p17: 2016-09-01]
Media_files/tutorial/assembly/8_connections_8.jpg

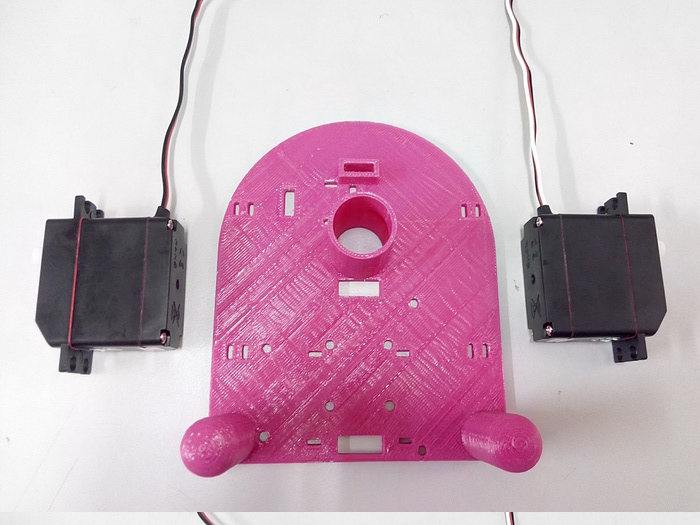
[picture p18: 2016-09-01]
Media_files/tutorial/assembly/2_motors_1.jpg

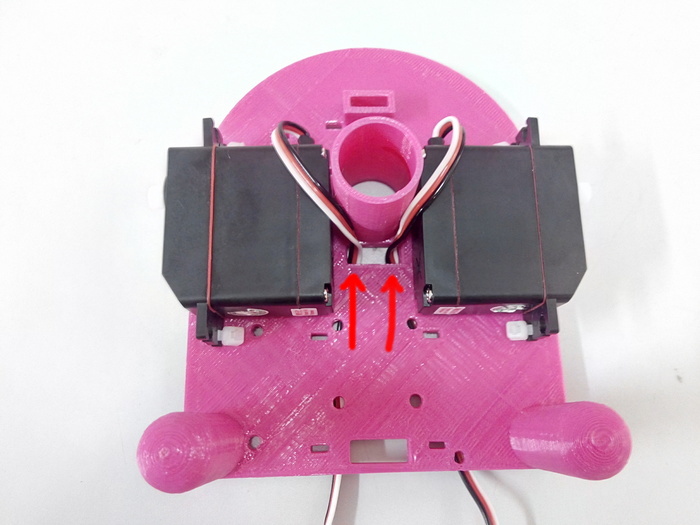
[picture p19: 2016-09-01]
Media_files/tutorial/assembly/2_motors_11.jpg

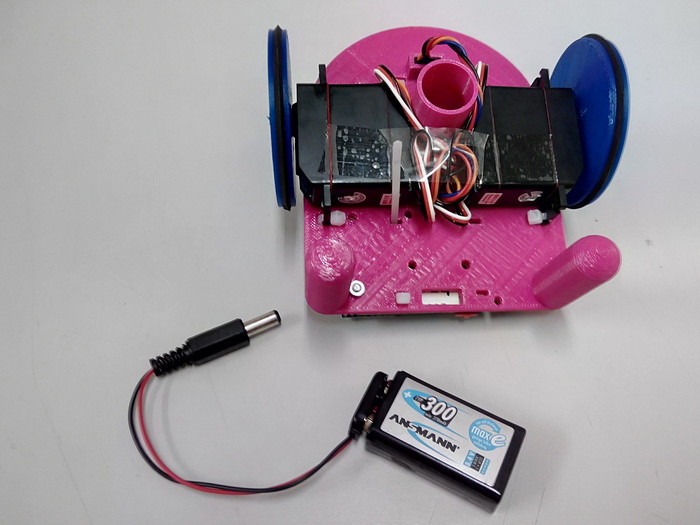
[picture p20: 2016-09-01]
Media_files/tutorial/assembly/10_battery_2.jpg

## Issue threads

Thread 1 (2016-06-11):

Definir el protocolo de comunicación entre biblioteca e intérprete

molins, 2016-06-11:
La [biblioteca](https://github.com/CRM-UAM/Phogo/wiki/Biblioteca) mandará comandos al [intérprete](https://github.com/CRM-UAM/Phogo/wiki/Interprete). Hay que definir el protocolo de comunicación entre ambos.

Debe establecerse el formato de los comandos y el listado de todos los posibles.

molins, 2016-06-15:
Ya se puede consultar en la [página del intérprete de la wiki](https://github.com/CRM-UAM/Phogo/wiki/Interprete)

Closed 2016-06-15.

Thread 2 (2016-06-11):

Elegir las licencias

molins, 2016-06-11:
Ahora mismo están elegidas dos licencias. Una para el código ([GNU General Public License Version 3](http://www.gnu.org/licenses/gpl-3.0.html)) y otra para el resto de material publicado ([CC BY-SA](https://creativecommons.org/licenses/by-sa/4.0/)).

Ambas son licencias libres pero a la vez restrictivas, en el sentido de que fuerzan a que las obras derivadas mantengan licencias libres. Son las licencias que más me gustan, pero está abierto a debate.

Closed 2016-11-02.

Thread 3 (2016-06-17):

decidir el modelo de comunicación

ChacheGS, 2016-06-17:
A los diseñadores @molins @CarlosGS
Veo dos alternativas:

1. Buffering: guardar las ordenes en un buffer
  * envio secuencial cuando se ha procesado el programa entero
  * si hay excepciones, no se procesa mas, y
  * no se abren conexiones innecesarias
  * si se manda, es que tiene sentido, y la conexion se abre y cierra limpiamente
2. Envio directo: sin buffer
  * no se procesa todo el programa antes de enviarlo
  * menor uso de memoria
  * se mantiene el socket BT abierto, aunque vaya a explotar
  * no se sabe cual es la ultima orden, y no se puede cerrar el socket en condiciones

molins, 2016-06-17:
Tiene que ser **la segunda**. Fallo mío que no está en la wiki explicado. Me lo apunto!

Como hay una función para **leer el sensor de ultrasonidos** (y más peligroso aún, **estructuras de control de flujo**) no se puede hacer con buffer (o no al menos de una forma razonable).

molins, 2016-06-17:
Si mi respuesta te satisface, cierra el issue, que queda más mono :+1:

ChacheGS, 2016-06-17:
Claro que se puede hacer con buffer, a no ser que lo esté entendiendo mal. Buffer en el ordenador de hará las veces de hub de comunicaciones, en el propio proceso que usen los niños.
Pseudocódigo:
```
func enviar_programa() {
    socket.conectar()
	while (not buffer.empty()) {
		instruccion = buffer.pop()
        socket.enviar(instruccion)
        ack = socket.recibir()
		if (not ack == 'OK') {
			break;
		}
	}
    socket.desconectar()
}
```

molins, 2016-06-17:
Imagina este pseudocódigo:

     if SensorUltrasonidos() > 10:
        Aanzar()
    else:
        Derecha()

¿Cómo quedaría la pila antes de mandarse al robot?

P.D.: Estoy en el móvil y no sé si este mensaje va a estar bien formateado…

ChacheGS, 2016-06-17:
Vale, me había perdido ese comando, me quedé en que todos devolvían 'OK/ERR'. Descartado el buffer.

Closed 2016-06-17.

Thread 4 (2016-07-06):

Renombrar las funciones

molins, 2016-07-06:
Por un fallo mío, toca renombrar las funciones. Como @ChacheGS es un tipo inteligente, está previsto. Ahora en inglés y siguiendo el estilo de Python para nombrar funciones.

```
Avanzar() --> forward()
Retroceder() --> back()
GirarDerecha() --> right()
GirarIzquierda() --> left()
EmpezarADibujar() --> pen_up()
DejarDeDibujar() --> pen_down()
LeerSensor() --> obstacle()
```

Closed 2016-07-06.

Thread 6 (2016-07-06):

Eliminar la dirección BT de cada línea

molins, 2016-07-06:
Que aparezca al principio de cada ejecución nos puede ser muy útil para depurar errores, pero que aparezca en cada línea puede confundir a los chavales o desviar su atención. Si pudiéramos quitarlo, sería fantástico de la muerte.

Closed 2016-07-06.

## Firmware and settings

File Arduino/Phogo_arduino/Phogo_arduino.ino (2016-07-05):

// This source file is part of the Phogo project
// https://github.com/CRM-UAM/Phogo
// Released under the GNU General Public License Version 3
// Club de Robotica-Mecatronica, Universidad Autonoma de Madrid, Spain

//--------------------------
// **** begin MISC *********
//--------------------------
// map() implementation modified for floating point operation
float mapf(float x, float in_min, float in_max, float out_min, float out_max) {
    return (x - in_min) * (out_max - out_min) / (in_max - in_min) + out_min;
}

//--------------------------
// **** begin LED **********
//--------------------------
#define LED_PIN 13
#define ON 1
#define OFF 0

void init_led() {
    pinMode(LED_PIN, OUTPUT);
}

void led(bool state) {
    digitalWrite(LED_PIN, state);
}

//--------------------------
// **** begin SERVO PEN ****
//--------------------------
#include <Servo.h>

Servo pen_servo;
#define PEN_SERVO_PIN 10
#define UP 180 // degrees
#define DOWN 140 // degrees

void pen_move(int deg) {
    pen_servo.attach(PEN_SERVO_PIN);
    pen_servo.write(deg);
    delay(500);
    pen_servo.detach(); // power down the servo after the target position has been reached
}

//--------------------------
// **** begin ULTRASOUND ***
//--------------------------
// Based on code by Robi.Wang
#define ULTRASOUND_TRIGGER_PIN 7
#define ULTRASOUND_ECHO_PIN 6

void init_ultrasound() {
    pinMode(ULTRASOUND_TRIGGER_PIN, OUTPUT);
    pinMode(ULTRASOUND_ECHO_PIN, INPUT);
    digitalWrite(ULTRASOUND_TRIGGER_PIN, LOW);
}

float measure_distance_cm() {
    digitalWrite(ULTRASOUND_TRIGGER_PIN, HIGH);
    delayMicroseconds(10);
    digitalWrite(ULTRASOUND_TRIGGER_PIN, LOW);
    long microseconds = pulseIn(ULTRASOUND_ECHO_PIN, HIGH, 20000); // Measures the duration of the input pulse (it is proportional to the time it takes for the sound to bounce back)
    return microseconds / 29. / 2.;
}

int measure_distance_cm_filtered(int nsamples) {
    float res = 0;
    int n = nsamples;
    while (n > 0) {
        float dist = measure_distance_cm();
        if (dist > 0) {
            res += dist;
            n--;
        }
        delay(10);
    }
    return res / nsamples;
}

//--------------------------
// **** begin IMU **********
//--------------------------
// Gyroscope/Accelerometer code derived from: MPU-6050 Short Example Sketch by Arduino User JohnChi
#define MPU6050_VCC_PIN A0
#define MPU6050_GND_PIN A1
#define MPU6050_SDA_PIN A3
#define MPU6050_SCL_PIN A2

#include <SoftwareWire.h> // Using a virtual I2C port and 5V power through two digital pins,
// allows to plug the gyroscope module directly into a row of pins, without the need for extra wires

SoftwareWire Wire(MPU6050_SDA_PIN, MPU6050_SCL_PIN);

const int MPU = 0x68; // I2C address of the MPU-6050

#define MPU6050_PWR_MGMT_1    0x6B
#define MPU6050_ACCEL_CONFIG  0x1C
#define MPU6050_GYRO_CONFIG   0x1B
#define MPU6050_SMPLRT_DIV    0x19
#define MPU6050_CONFIG        0x1A

int16_t AcX, AcY, GyZ;
int16_t AcX_raw, AcY_raw, GyZ_raw;
int16_t AcXoffset, AcYoffset, GyZoffset;
float GyZ_integral, rotation;
unsigned long IMU_last_ts = 0;

void IMUwriteReg(byte reg, byte val) {
    Wire.beginTransmission(MPU);
    Wire.write(reg);
    Wire.write(val);
    Wire.endTransmission(true);
}

void init_IMU() {
    pinMode(MPU6050_VCC_PIN, OUTPUT); // Turn on the power for the Gyroscope module, using two arduino pins
    pinMode(MPU6050_GND_PIN, OUTPUT); // This is possible since the MPU6050 IMU can work with very little power
    digitalWrite(MPU6050_VCC_PIN, HIGH);
    digitalWrite(MPU6050_GND_PIN, LOW);

    Wire.begin(); // Initialise the I2C port
    Wire.setTimeout(10);

    for (int i = 0; i < 3; i++) { // Reset the IMU a few times
        IMUwriteReg(MPU6050_PWR_MGMT_1, bit(7));   // DEVICE_RESET to 1 (D7=1)
        delay(100);
    }
    IMUwriteReg(MPU6050_PWR_MGMT_1, bit(0) | bit(1));  // set clock source to Z Gyro (D0=D1=1, D2=0) and set SLEEP to zero (D6=0, wakes up the MPU-6050)
    IMUwriteReg(MPU6050_ACCEL_CONFIG, bit(3) | bit(4));  // set sensitivity to +-16G (D3=1, D4=1) and disable high pass filter (D0,D1,D2=0)
    IMUwriteReg(MPU6050_GYRO_CONFIG, bit(3) | bit(4));  // set sensitivity to +-2000deg/s (D3=1, D4=1)
    IMUwriteReg(MPU6050_SMPLRT_DIV, 0);  // set sampling rate to 1khz (1khz / (1 + 0) = 1000 Hz)
    IMUwriteReg(MPU6050_CONFIG, bit(0) | bit(5));  // disable digital low pass filter (D0=D1=D2=0) and EXT_SYNC to GYRO_ZOUT (D3=D4=0, D5=1)
}

bool read_IMU() {
    int16_t new_AcX, new_AcY, new_GyZ;
    Wire.beginTransmission(MPU);
    Wire.write(0x3B);  // starting with register 0x3D (ACCEL_YOUT_H)
    Wire.endTransmission(false);
    Wire.requestFrom(MPU, 14, true); // request a total of 14 registers

    // Receive and decode the response
    new_AcX = Wire.read() << 8 | Wire.read(); // 0x3B (ACCEL_XOUT_H) & 0x3C (ACCEL_XOUT_L)
    new_AcY = Wire.read() << 8 | Wire.read(); // 0x3D (ACCEL_YOUT_H) & 0x3E (ACCEL_YOUT_L)
    for (int i = 0; i < 8; i++) Wire.read(); // Discard 0x3F-0x46
    new_GyZ = Wire.read() << 8 | Wire.read(); // 0x47 (GYRO_ZOUT_H) & 0x48 (GYRO_ZOUT_L)

    bool updated = (AcX_raw != new_AcX) || (AcY_raw != new_AcY) || (GyZ_raw != new_GyZ); // Check if value has changed

    AcX_raw = new_AcX;
    AcY_raw = new_AcY;
    GyZ_raw = new_GyZ;
    AcX = AcX_raw - AcXoffset;
    AcY = AcY_raw - AcYoffset;
    GyZ = GyZ_raw - GyZoffset;
    return updated;
}

void calibrate_IMU() {
    // Measure IMU sensor offsets (the robot must remain still)
    AcXoffset = 0;
    AcYoffset = 0;
    GyZoffset = 0;
    for (int i = 0; i < 10; i++) {
        while (read_IMU() == false) delay(10);
        AcXoffset += AcX_raw;
        AcYoffset += AcY_raw;
        GyZoffset += GyZ_raw;
    }
    AcXoffset /= 10;
    AcYoffset /= 10;
    GyZoffset /= 10;
    GyZ_integral = 0;
}

void integrate_IMU() {
    while (!read_IMU());
    unsigned long ts = micros();
    float dt = ((float)(ts - IMU_last_ts)) / 1000000.; // seconds
    if (dt > 0) {
        if (dt < 0.5) GyZ_integral += GyZ * dt;
        IMU_last_ts = ts;
        rotation = GyZ_integral * 2000. / 32768.; // +-2000 deg/s sensitivity; +-2^15 full scale
    }
}

void offset_IMU(float deg) {
    GyZ_integral += deg * 32768. / 2000.;
}

void zero_IMU() {
    GyZ_integral = 0;
}

//--------------------------
// **** begin MOTORS *******
//--------------------------
Servo L_servo, R_servo;
#define L_SERVO_MOTOR_PIN 8
#define R_SERVO_MOTOR_PIN 9
unsigned long motors_last_ts = 0;

#define VELOCITY_FORWARD 15
#define VELOCITY_BACKWARD -15
#define REAL_VELOCITY 100 // mm/s

int limit_angle(int deg) {
    return min(max(deg, 0), 180);
}

void calibrate_motors() {
    L_servo.attach(L_SERVO_MOTOR_PIN);
    R_servo.attach(R_SERVO_MOTOR_PIN);
    L_servo.write(90); // Set 90deg target angle in order to calibrate the motors
    R_servo.write(90); // The potentiometer for each servo should be tuned so the motor is stopped
    delay(10000);
    L_servo.detach();
    R_servo.detach();
}

void actuate_motors(float distanceGoal, float targetAngleDeg) {
    L_servo.attach(L_SERVO_MOTOR_PIN);
    R_servo.attach(R_SERVO_MOTOR_PIN);

    distanceGoal *= 10; // Convert from cm to mm

    float velocity = VELOCITY_FORWARD * (distanceGoal > 0) + VELOCITY_BACKWARD * (distanceGoal < 0);
    float distance_integral = 0;

    offset_IMU(-targetAngleDeg);
    while (1) {
        integrate_IMU();
        unsigned long ts = micros();
        float dt = ((float)(ts - motors_last_ts)) / 1000000.; // seconds
        if (dt > 0) {
            if (dt < 0.5) distance_integral += 48 * dt;
            motors_last_ts = ts;
        }
        L_servo.write(limit_angle(90 - velocity - 0.5 * rotation));
        R_servo.write(limit_angle(90 + velocity - 0.5 * rotation));
        if (distanceGoal == 0) {
            if (abs(rotation) < 10) break;
        } else {
            if (distance_integral >= abs(distanceGoal)) break;
        }
    }

    L_servo.detach();
    R_servo.detach();

    unsigned long ts = millis();
    while (millis() - ts < 500) integrate_IMU(); // integrate any remaining motion
}

//--------------------------
// ****  BATTERY LEVEL  ****
//--------------------------
/*#define LOW_BAT_THRESHOLD 5050 // mV
#define BATTERY_CHECK_INTERVAL 10000 // ms

long battery_last_measure = 0;
bool low_battery = false;

long readVcc() {
    long result; // Read 1.1V reference against AVcc
    ADMUX = _BV(REFS0) | _BV(MUX3) | _BV(MUX2) | _BV(MUX1);
    delay(2); // Wait for Vref to settle
    ADCSRA |= _BV(ADSC); // Convert
    while (bit_is_set(ADCSRA, ADSC));
    result = ADCL;
    result |= ADCH << 8;
    result = 1126400L / result; // Back-calculate AVcc in mV
    return result;
}

void checkBattery() {
    if ((millis() - battery_last_measure) > BATTERY_CHECK_INTERVAL) {
        battery_last_measure = millis();
        if (readVcc() < LOW_BAT_THRESHOLD) {
            actuate_motors(0, 0); //stop
            low_battery = true;
        }
    }
}*/

//--------------------------
// ****    MAIN         ****
//--------------------------
void setup() {
    init_led();
    led(ON);
    //checkBattery();
    //if (!low_battery) {
    String msg = "READY (";
    delay(400);
    Serial.begin(19200);
    init_IMU();
    pen_move(UP);
    init_ultrasound();
    calibrate_IMU();
    while (Serial.available()) Serial.read(); // Flush input buffer
    msg += readVcc();
    msg += ")";
    Serial.println(msg);
    //}
    led(OFF);
}

void loop() {

    /*if (low_battery == true) {
        led(OFF);
        delay(200);
        led(ON);
        delay(800);
    } else {*/
    //checkBattery();
    if (Serial.available()) {
        String line = Serial.readStringUntil('\n');
        line.trim(); // Skip initial garbage (\n \r and spaces)
        if (line.length() >= 2) {
            String command = line.substring(0, 2); // Extract the first two letters
            String value = line.substring(2); // Extract the rest of the message
            led(ON);
            if (command == "PD") {
                pen_move(DOWN);
                Serial.println("OK");

            } else if (command == "PU") {
                pen_move(UP);
                Serial.println("OK");

            } else if (command == "FD") {
                actuate_motors(value.toInt(), 0);
                Serial.println("OK");

            } else if (command == "BK") {
                actuate_motors(-value.toInt(), 0);
                Serial.println("OK");

            } else if (command == "RT") {
                actuate_motors(0, -value.toInt());
                Serial.println("OK");

            } else if (command == "LT") {
                actuate_motors(0, value.toInt());
                Serial.println("OK");

            } else if (command == "OE") {
                int dist = measure_distance_cm_filtered(10);
                Serial.println(dist);

            } else if (command == "CA") {
                calibrate_motors();
                Serial.println("OK");

            } else {
                Serial.println("ERROR: UNKNOWN COMMAND");
            }
            led(OFF);
        }
    }
    //integrate_IMU(); // do not integrate rotations while the robot is static
    //}
}

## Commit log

2016-06-16 Work in progress with the 3D printed chassis
    [robot_chassis.scad]
2016-06-16 Included ultrasonic sensor and board reference
    [robot_chassis.scad]
2016-06-16 First version of the chassis
    [robot_chassis.scad, robot_chassis.stl]
2016-06-16 Detalles de lo existente
2016-06-20 empiezo con el BT
2016-06-21 Añadido \n final para el envio de ordenes
2016-06-21 Algo más de validacion y control de errores
2016-06-21 A falta de pruebas de BT (y puede que *algo* de documentación xD), lo doy por terminado
2016-06-21 WIP with the gyroscope and robot firmware
2016-06-22 Increased pen diameter and reduced robot length
    [build_plate.scad, robot_chassis.scad]
2016-06-22 Renamed files and linked robot picture in the README
    [robot.scad, robot.stl]
2016-06-22 Added pen holder
    [pen_holder.stl, robot.scad, robot.stl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]
2016-06-23 Formateo el codigo por legibilidad
2016-06-23 AHora me he leido la documentacion xD
2016-06-23 Added motor initialisation
2016-06-24 Cambiada la forma de obtener las MAC de BT
2016-06-27 Repositioned mini-servo and arduino board. Increased pen holder tolerances. Also, the text font is now bold in order to improve readability.
    [pen_holder.stl, robot.scad, robot.stl]
2016-06-27 Empiezo una herramienta de configuracion para hacer usuarios independientes, facilmente accesibles para ssh y la magia de las MACs BT
2016-06-27 One MAC more!
    “Another MAC, another destiny.
    This never-ending road to Calvary;
    These men who seem to know my crime
    Will surely come a second time.
    One MAC more!”
    Geek point to anyone guessing.
2016-06-28 Added motor calibration as a command, improved gyroscope integration
2016-06-28 phogo.sh parece que funciona
2016-06-30 Herramienta de debug. Solo lee desde BT
2016-07-04 Codigo para dibujar estrellas y codigo para comprobar la bateria del arduino
2016-07-05 Increased tolerances
    [pen_holder.stl, robot.scad, robot.stl]
2016-07-05 MACs de los robots
2016-07-05 Lo de la bateria no prospera
2016-07-07 Bug fix
    Y se añade versión justificada, a gusto de @ChacheGS
2016-07-14 Añadido un timeout mejor para los comandos
2016-09-01 Added assembly pictures
2016-09-01 Renamed assembly pictures
2016-09-01 Renamed files
    [phogo.scad, phogo.stl]
